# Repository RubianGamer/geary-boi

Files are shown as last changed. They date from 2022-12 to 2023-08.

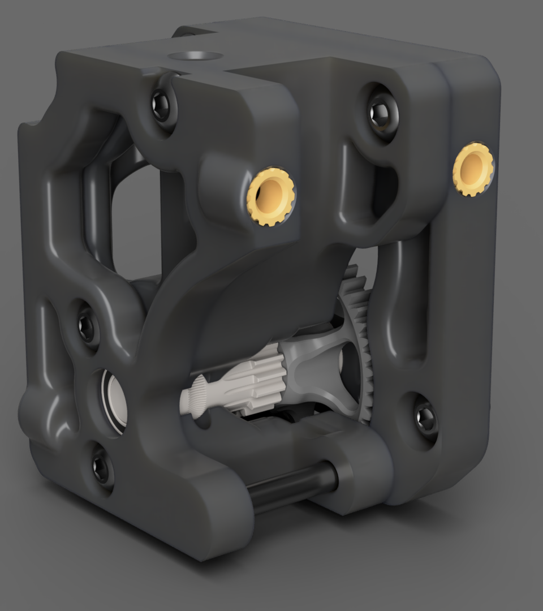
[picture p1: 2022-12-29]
renders/tall version/geary_boy_extruder_4.png

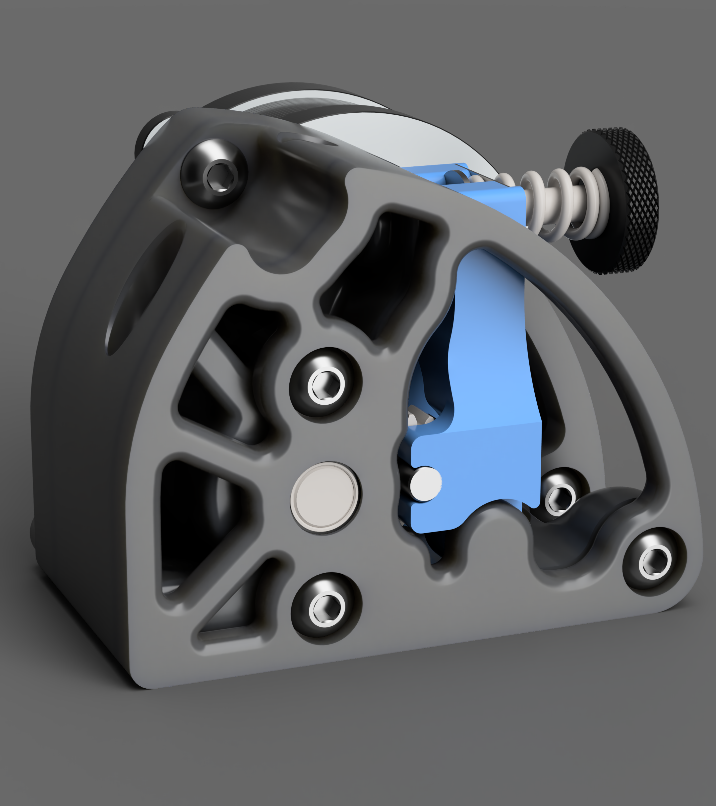
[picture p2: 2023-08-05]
renders/low version/geary_boi_low_front.png

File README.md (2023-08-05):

# Geary Boi

Geary Boi is a BMG based extruder with a small footprint to fit on small toolheads.

render_front

# features

- 8 mounting holes on sides and bottom
- compact and lightweight design
- super tight tolerance housing avalible for excelent performance with TPU (tested with 82A TPU at 100mm/s)
- supports both 10 tooth and 8 tooth gear nema14 motors

- seperate lower but wider version avalible

# Discord

for more info or questions about the extruder, or other 3d printing/printer related things, feel free to joing the discord server.
https://discord.gg/2XBTuWrQu5

# patreon

if you want to support my work, feel free to join my patreon
https://www.patreon.com/RubianGamer

# renders

render_front

render_back

render_back2

render_side

render_low_front

render_low_rear

render_low_side

# prints

82A TPU at 100mm/s (8mm/s^2)
TPU_print

woodgrain test print
woodgrain

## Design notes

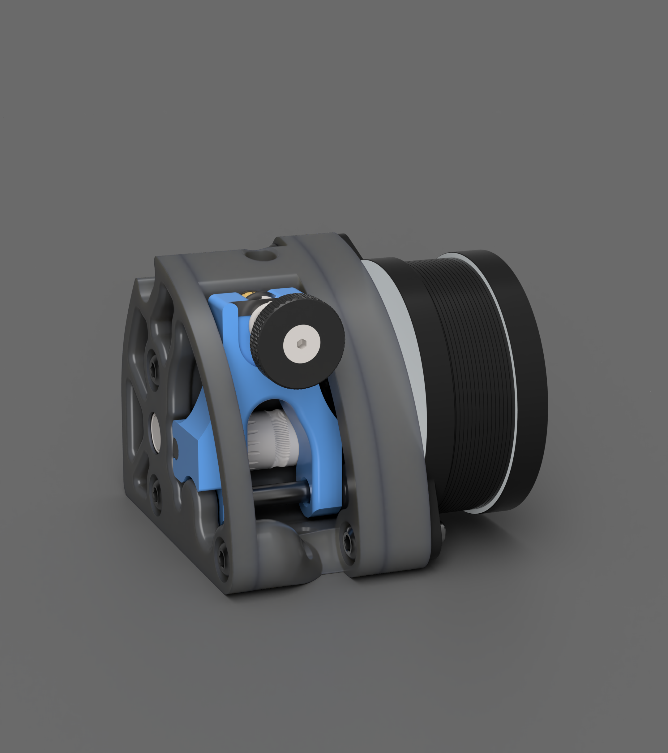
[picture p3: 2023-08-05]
renders/low version/geary_boi_low_side.png

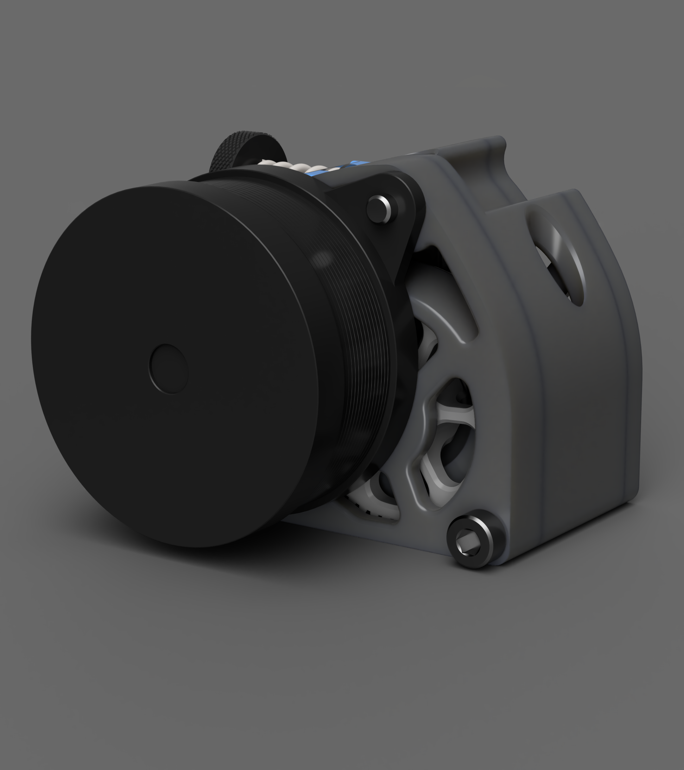
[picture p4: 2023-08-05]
renders/low version/geary_boi_low_rear.png

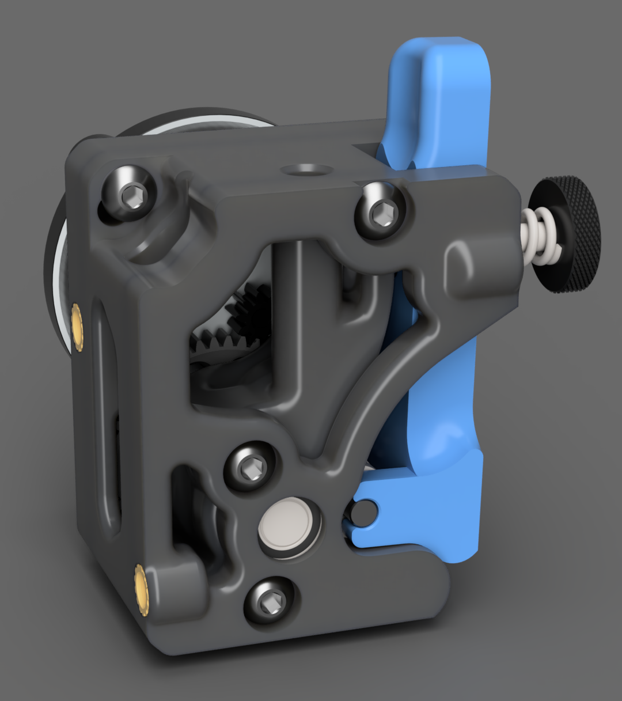
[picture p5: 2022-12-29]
renders/tall version/geary_boy_extruder.png

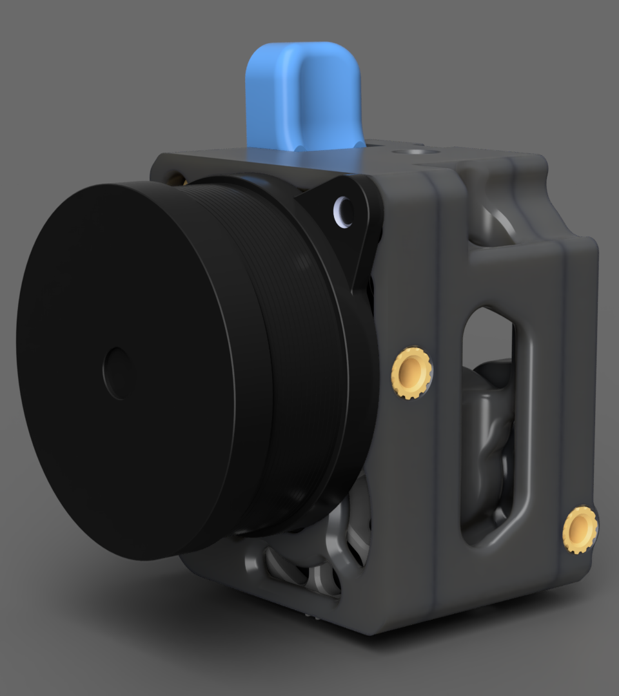
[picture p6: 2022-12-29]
renders/tall version/geary_boy_extruder_2.png

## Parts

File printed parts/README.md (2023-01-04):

# print settings

print out of ASA or better (ABS works but not recommended)
use a 0.4mm nozzle or smaller with 0.2 or 0.1mm layer height
3 perimiters (or 1.2mm) 5 top/bottom (1mm) 30% cubic infill
no supports are needed for any of the parts

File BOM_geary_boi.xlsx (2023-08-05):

BOM Geary Boi
category | part name | quantity | obtained | source | notes
hardware | M3 heatset | 9 |  | aliexpress (https://aliexpress.com/item/1005002530005649.html) | needs to be 5mm in diameter and 4mm in length
hardware | M3x6 BHCS | 5 |  | schrauben-expert (https://schrauben-expert.de/) | other types of heads will work, as long as they are under 2mm in height
hardware | M3x12 BHCS | 1 |  |  | interchangable for a M3x12 SHCS
extruder hardware | BMG internals | 1 |  | aliexpress (https://aliexpress.com/item/4000021186440.html) | any standard BMG internals kit will work, got minimal woodgrain with these.
extruder hardware | moons 8 tooth stepper or LDO-36STH17-1004AH(G8T) | 1 |  | aliexpress (https://aliexpress.com/item/32653413820.html) | 8 tooth moons stepper is best choice 36STH17-1004AH(G8T) is a good alternative, but runs hotter other nema14 pancakes with 8 or 10 tooth gears will work as well
printed parts | stepper mount | 1 |  | printed | print out of ASA or PCCF/GFPC or any other high temp material for best results. ABS works, but tends to melt near the stepper print either the normal or low tolerance version of the main body. Low tolerance is prefered, especially for TPU
printed parts | main body | 1
printed parts | face plate | 1
printed parts | latch | 1
an additonal M3x3 BHCS and M3x12SHCS are required for the low version

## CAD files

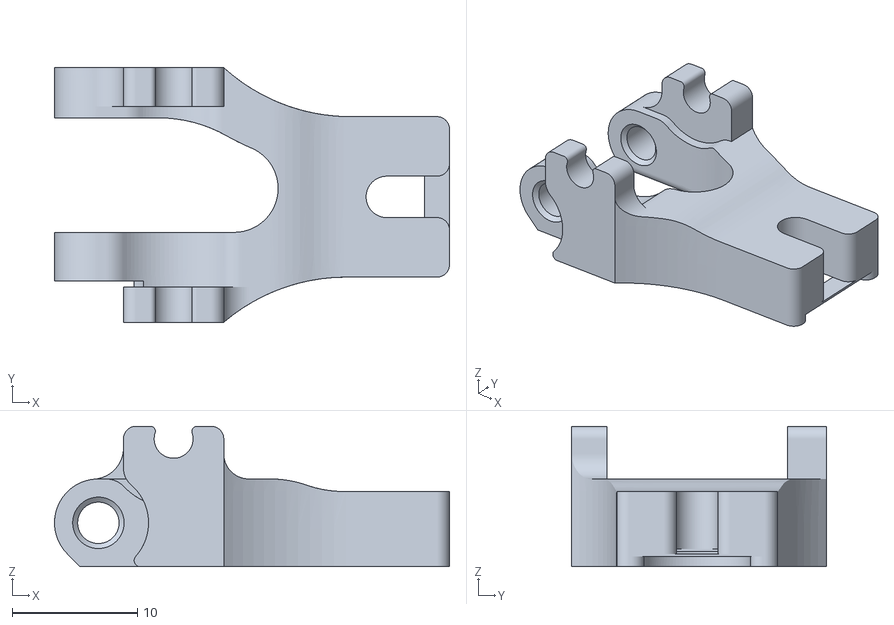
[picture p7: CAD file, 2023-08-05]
printed parts/low version/latch arm.stl
31.5 x 20.3 x 11.2

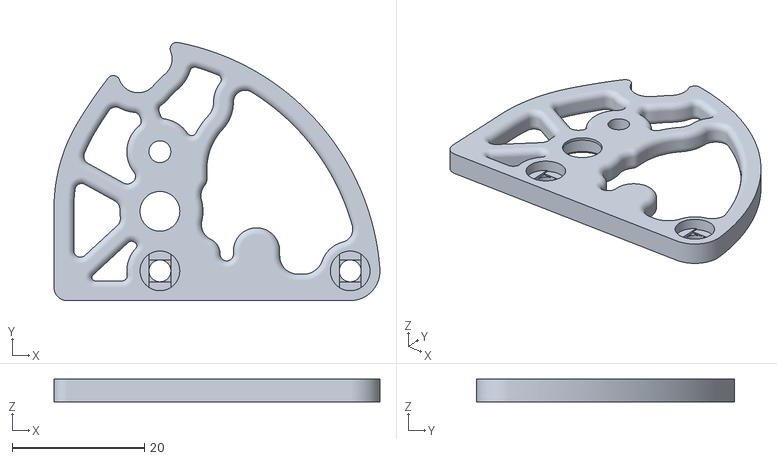
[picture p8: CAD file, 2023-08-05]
printed parts/low version/melty specific parts/face plate (melty).stl
49.2 x 39.0 x 3.40

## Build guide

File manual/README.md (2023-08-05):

1) put heatsets into all the parts (9 total), reference CAD if its not clear where they all go. clear up the filament path using a 2mm allen key if needed.
2) screw the stepper to the stepper mount using a M3x6 BHCS in the bottom right corner, but dont fully tighten it.
3) press fit the BMG bearing into the stepper mount and put the drivetrain with filament drive gear in the bearing.
4) adjust the stepper so the gears mesh properly, fully tighten down the M3x6 BHCS after adjustments are made.
5) slide the main body over the gears, making sure the gears dont rub, and mount it using a M3x6 BHCS at the top right.
6) screw in the stepper using a M3x15 BHCS at the top left (oval hole).
7) insert ⌀3mm 24mm long steel shaft into the pivot point of the latch until 3mm sticks out of the left side seen from the bottom of the part.
8) lubricate needle bearings, slide them onto 20mm shaft, slide on BMG idler gear and press fit the assambly into idler arm.
9) insert idler arm assamby into main body with the long side of the latch pin facing the stepper into 3mm hole at the bottom right. 
10) press fit bearing into the face plate, them mount it to the front of the main body.
11) put spring over thumbscrew, cap off with washer, and insert though latch arm and screw into the main body.

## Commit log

2023-01-04 pre oriented STL files
2023-01-04 added print settings
2023-01-04 updated BOM
    [BOM_geary_boi.xlsx]
2023-01-04 added print pictures
2023-01-23 tweaked filament inlet
2023-08-05 added low version
    added low verion
    [BOM_geary_boi.xlsx, face plate (melty).stl, latch arm.stl]
